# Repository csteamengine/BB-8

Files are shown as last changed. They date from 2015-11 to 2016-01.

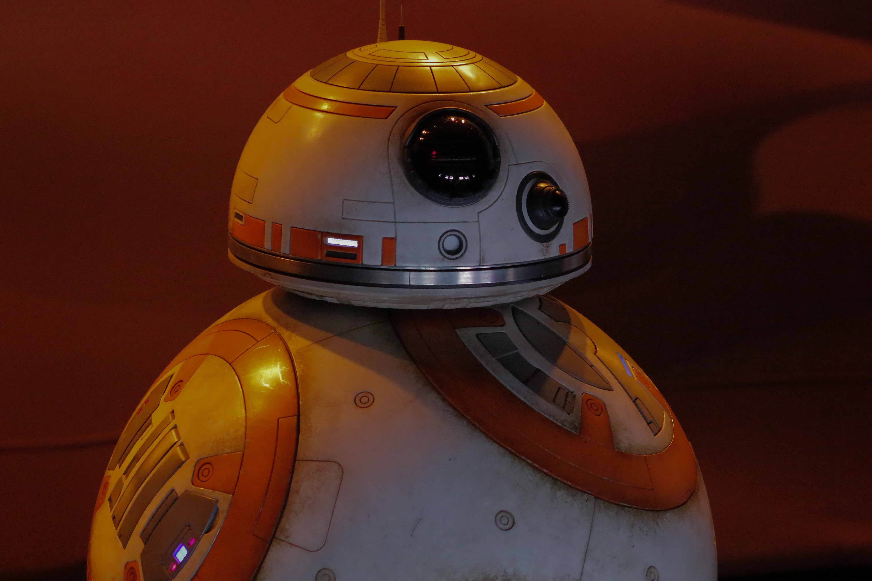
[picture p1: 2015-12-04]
Images/BB-8Reference.jpg

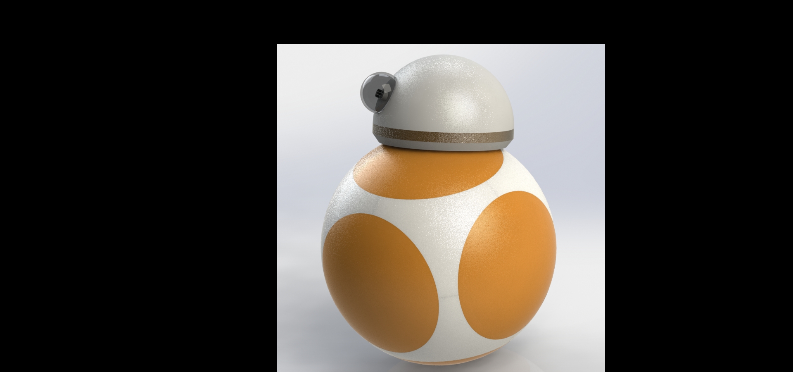
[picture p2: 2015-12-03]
Images/BB-8Early.JPG

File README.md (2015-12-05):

# BB-8
## Our version of BB-8 from Star Wars Episode VII
BB-8 from Star Wars Episode VII, The Force Awakens

For this project, we are attempting to build our own BB-8 as seen in the Star Wars Episode VII. He is a rolling droid with a head that can swivel around as he rolls, without falling off. 

To accomplish this, we used the following hardware...
```
Raspberry Pi 2 B+
2 DC gear motors + wheels
3 servos for head control
Old 12" Globe (main body) //We are working on getting a 3D printed body. Currently designing it.
Strong Magnets
Ball Bearing Casters
Foam Hemisphere for the head
Other Structural pieces of your choice (Ex// K'NEX or popsicle sticks)
Other Items for Decoration
Paint of your choice
```
We used [this](http://www.amazon.com/gp/product/B00GLO5SMY?psc=1&redirect=true&ref_=ox_sc_act_title_1&smid=A3P9EAC3KD93H7) chassis and motor combo.

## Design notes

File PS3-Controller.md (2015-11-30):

#PS3 Controller

The $ denotes the beginning of a line of code to be entered in the Terminal. 
First make sure your Pi is up to date (This may take a while depending on your pi):
	
	$sudo apt-get update
	
Then make install the bluetooth dongle support. This is different for each dongle so I will let you do that part.
There are tutorials all over the place explaining what to do.

Next install the bluetooth support (Drivers, compilers and such) this one will take a long time so get comfortable:   

	$ denotes a new line. this first one is a long line.
	$sudo apt-get install bluez-utils bluez-compat bluez-hcidump checkinstall libusb-dev libbluetooth-dev joystick
      
Once this is done you will need to download and compile the controller utility:

	$wget http://www.pabr.org/sixlinux/sixpair.c
    	$gcc -o sixpair sixpair.c -lusb

Next connect the PS3 controller to the Pi using the USB cable and type the following
    
    	$sudo ./sixpair

If this is successful, it will return something like this:

	Current Bluetooth master: 00:10:60:57:15:C7
 	Setting master bd_addr to: 00:10:60:57:15:C7 

If no controller is connected, a message will pop up saying "No controller found on USB busses". In my experience I only     needed to run the sudo ./sixpair command once for each controller, as long as you haven't reset it. Now run the following 		to download sixad, the controller manager.
    
    	$wget http://sourceforge.net/projects/qtsixa/files/QtSixA%201.5.1/QtSixA-1.5.1-src.tar.gz
    	$sudo tar xfvz QtSixA-1.5.1-src.tar.gz
    	$cd QtSixA-1.5.1/sixad
    	$sudo make
    	$sudo mkdir -p /var/lib/sixad/profiles
    	$sudo checkinstall

Once that is done, run the following to allow the controller mangager to run at boot. Now when you reboot the Pi, sixad will automatically run.

	$sudo update-rc.d sixad defaults
#PS3 Controller
Finally, unplug the controller and reboot the system.

	$sudo reboot

Once it is up and running again, sixad will already be running so all you have to do is press the PS button. If it does not connect or doesnt recognize it, first try restarting sixad.

    	$sudo sixad --stop
    	$sudo sixad --start
    
At this point it will prompt you to press the PS button. When you do so it will display this if it connected successfully.
This will be displayed on the screen.

	sixad-bin[2535]: started
	sixad-bin[2535]: sixad started, press the PS button now
	sixad-bin[2535]: unable to connect to sdp session
	sixad-bin[2535]: Connected Sony Computer Entertainment Wireless Controller

If it still wont connect then try plugging the controller in again and running.

	$sudo ./sixpair

Each time you start the pi, you simply have to press the PS button on the controller to connect it, as long as you ran the update -rc command above. However if you want to connect a second controller on boot up, in the terminal just type 
	$sixad --stop
	$sixad --start
Then press the PS button on the second controller.

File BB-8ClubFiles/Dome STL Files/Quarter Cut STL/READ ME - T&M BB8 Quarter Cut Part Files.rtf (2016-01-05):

For those with smaller X & Y build areas, like the FlashForge, Dremel, MakerBot Mini. Tiny has developed these Quarter Cut pieces.

These work just like the regular pieces, however instead of being 3 pieces to make a complete part, such as Dome Ring, Dome Skirt or even the Dome Panels, it requires you to print all 4 pieces.

The Dome Ring, you will notice is just 1 (one) STL part file, however you will need to print the file 4 times. This is indicated in the file name of the part by the x4 nomenclature.

Where as the Dome Skirt is actually only 2 (two) STL part files, and you will print each of those twice (x4). This is indicated in the file name of the part by the x2 nomenclature.

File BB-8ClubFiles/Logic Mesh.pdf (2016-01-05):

LED Panel Mesh Dome

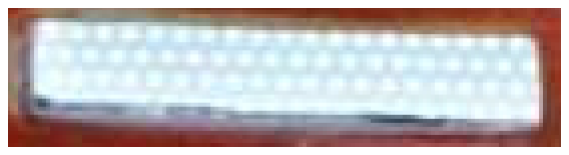
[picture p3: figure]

Approx. 23mm x 4mm

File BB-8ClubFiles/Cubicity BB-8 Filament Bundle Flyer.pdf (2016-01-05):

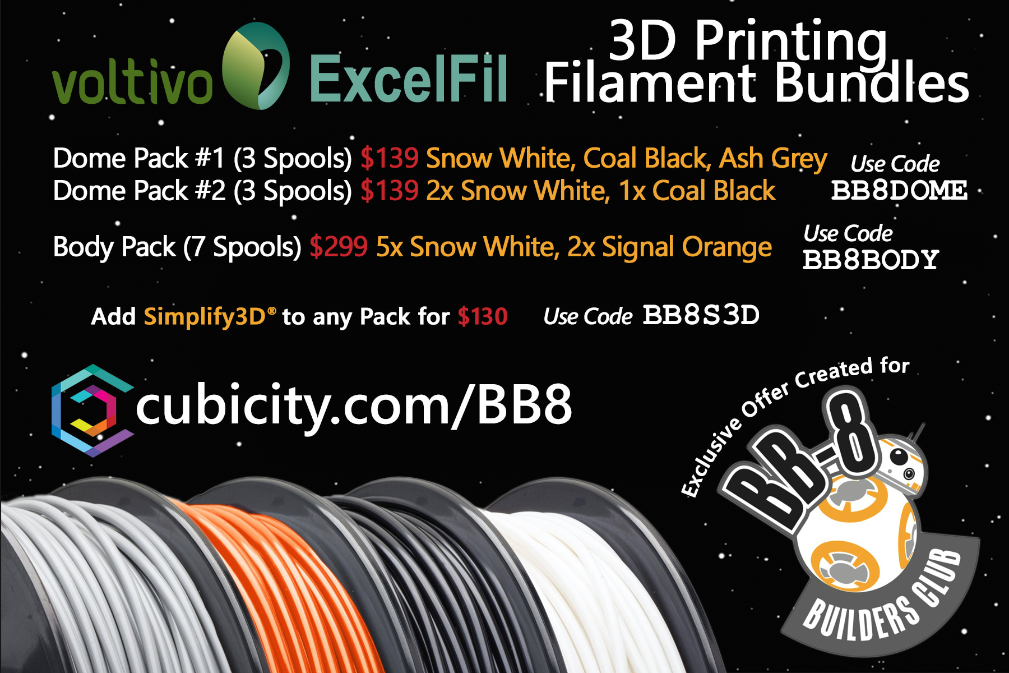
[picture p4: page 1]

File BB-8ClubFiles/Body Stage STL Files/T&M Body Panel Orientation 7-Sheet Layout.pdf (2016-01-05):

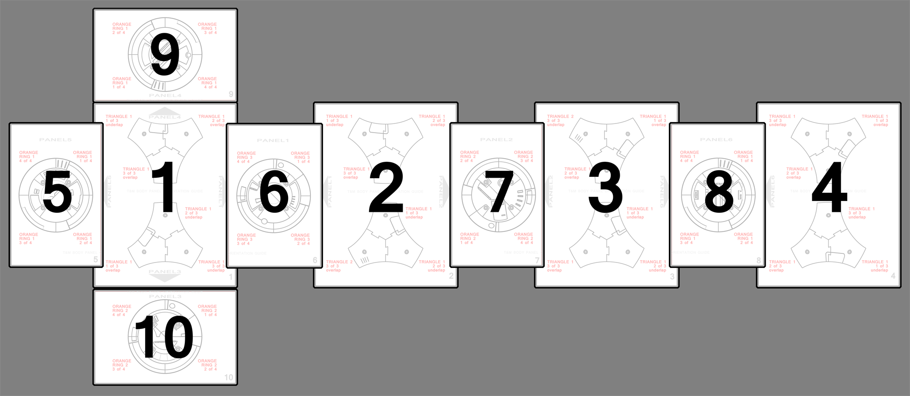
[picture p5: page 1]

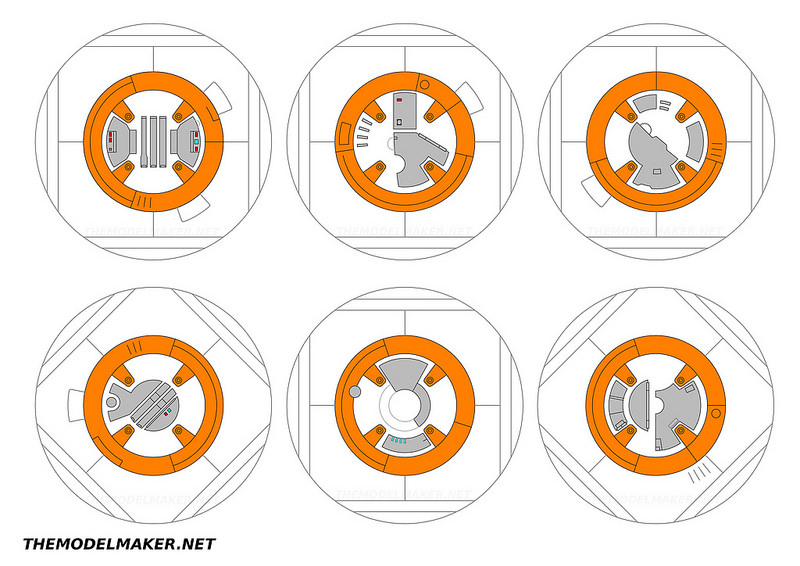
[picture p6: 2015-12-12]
Images/BB-8Panels.jpg

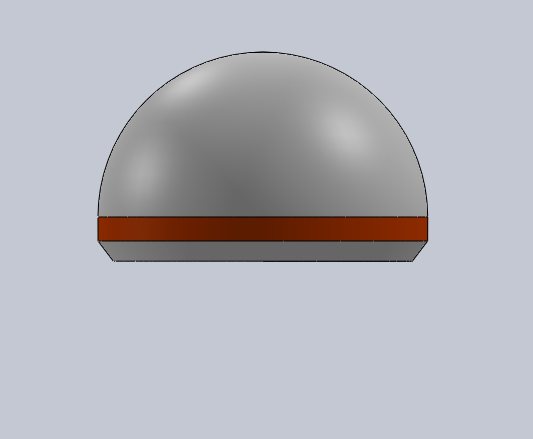
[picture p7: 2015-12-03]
Images/CAD3.PNG

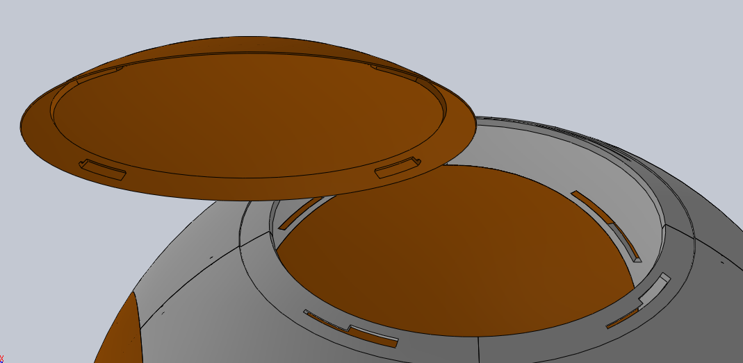
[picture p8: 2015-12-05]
Images/LockingMechanism.PNG

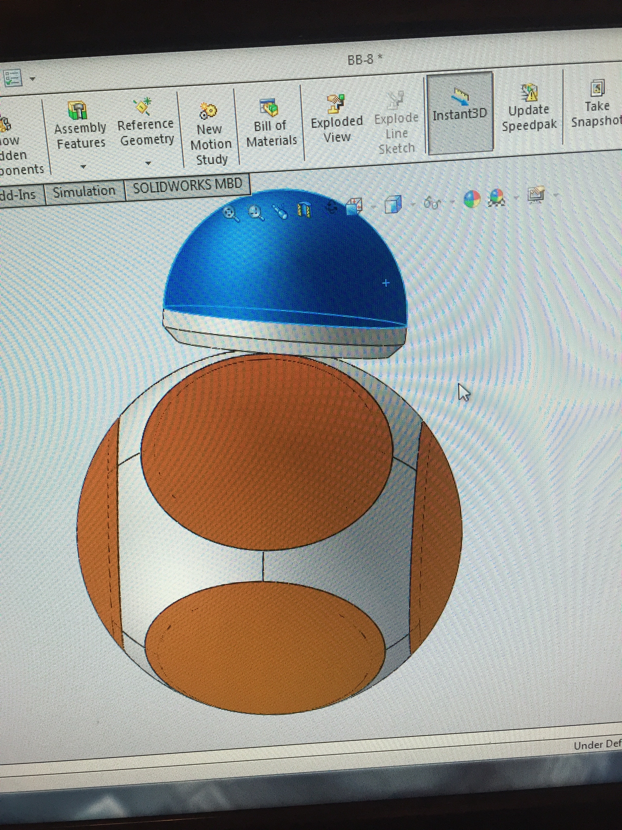
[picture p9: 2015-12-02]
Images/CAD1.jpg

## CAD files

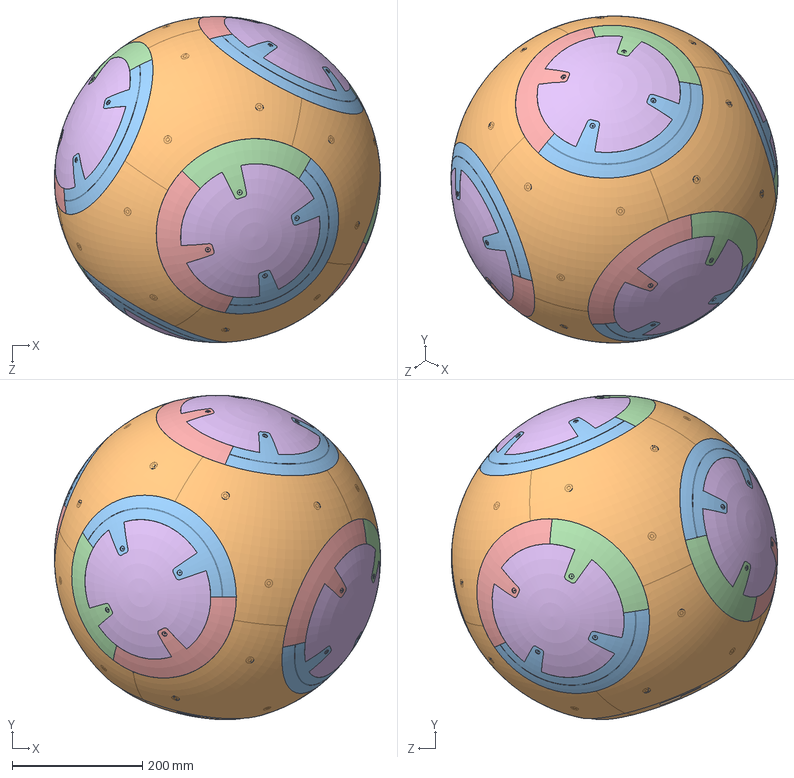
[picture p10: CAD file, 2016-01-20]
CAD/BB-8Test.SLDASM
499.8 x 497.2 x 499.8 mm
BB-8InnerShell x 4
BB-8Shell2 x 8
BB-8Shell1 x 5
BB-8Shell4 x 5
BB-8Shell5 x 5
BB-8Shell6 x 5
BB-8InnerShellTop x 4

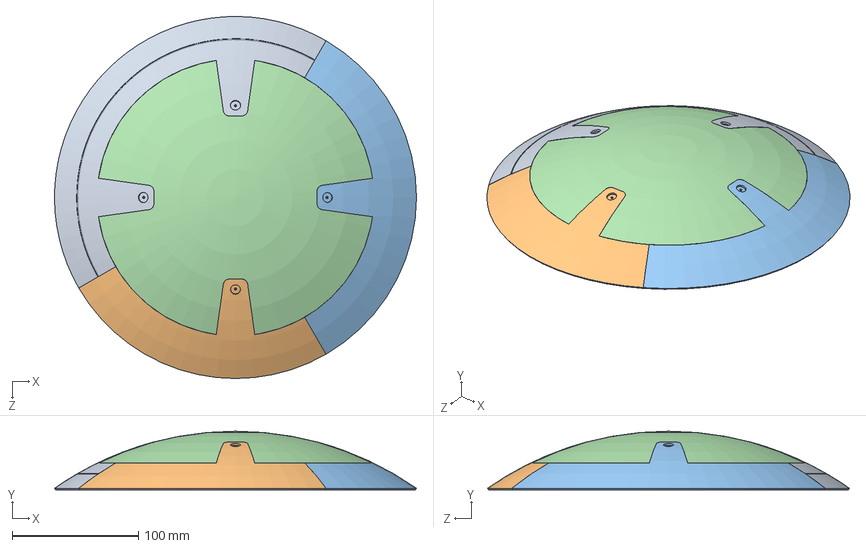
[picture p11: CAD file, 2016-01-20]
CAD/BB-8Panel.SLDASM
286.8 x 46.4 x 286.8 mm
BB-8Shell1
BB-8Shell4
BB-8Shell5
BB-8Shell6

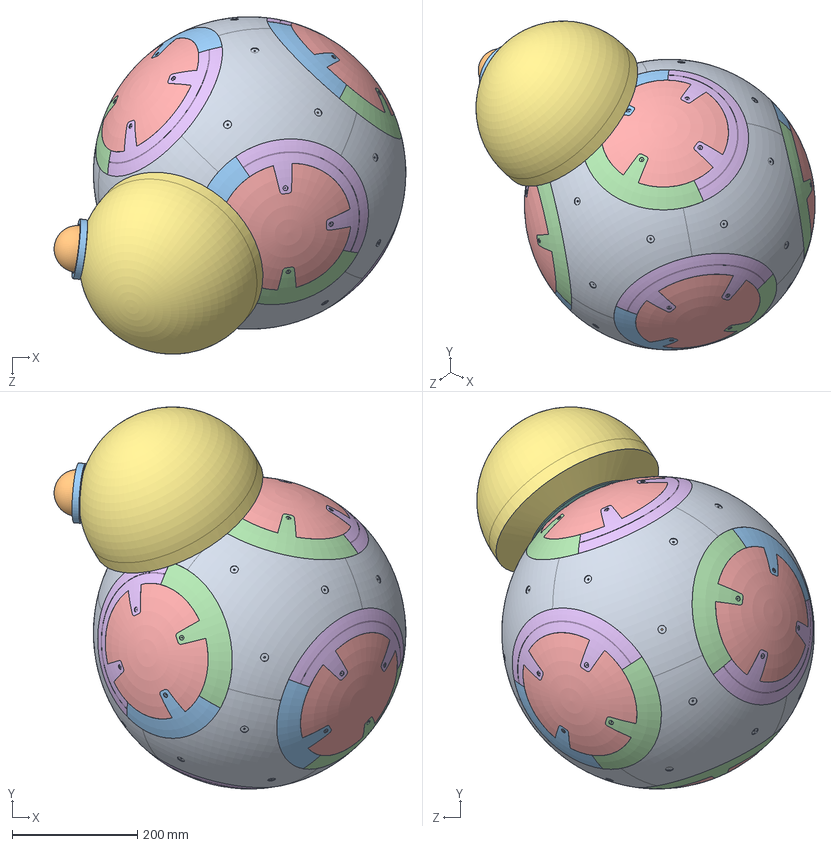
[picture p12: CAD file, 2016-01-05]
CAD/BB-8.SLDASM
562.8 x 611.2 x 539.8 mm
BB-8Shell2 x 8
BB-8Shell3 x 12
BB-8Shell4 x 6
BB-8Shell5 x 6
BB-8Shell6 x 6
BB-8Shell1 x 6
BB-8Head
BB-8HeadBottom
Ball Bearing x 4
BB-8Eye
BB-8EyeCap
Ball-Bearing-Cap x 4

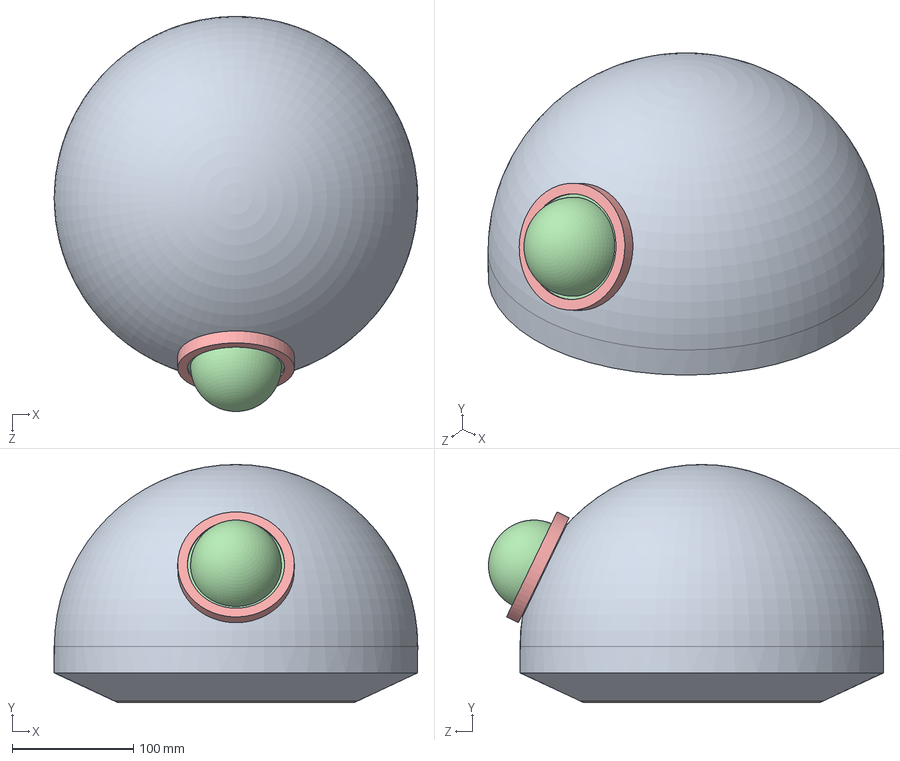
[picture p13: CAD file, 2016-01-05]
CAD/BB-8Head.SLDASM
300.0 x 196.4 x 325.9 mm
BB-8Head
BB-8HeadBottom
Ball Bearing x 4
BB-8Eye
BB-8EyeCap
Ball-Bearing-Cap x 4

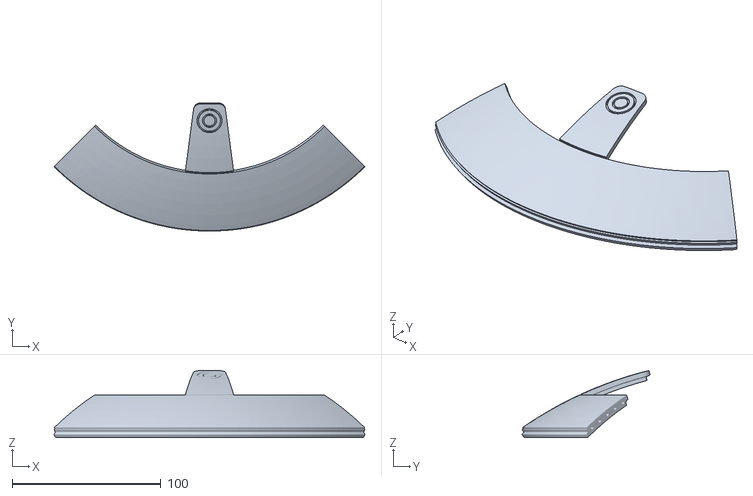
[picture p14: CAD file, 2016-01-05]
BB-8ClubFiles/Body Stage STL Files/Orange Rings/Orange Ring 1 V506mm 4 of 4 -1mm.stl
208.8 x 86.1 x 45.0

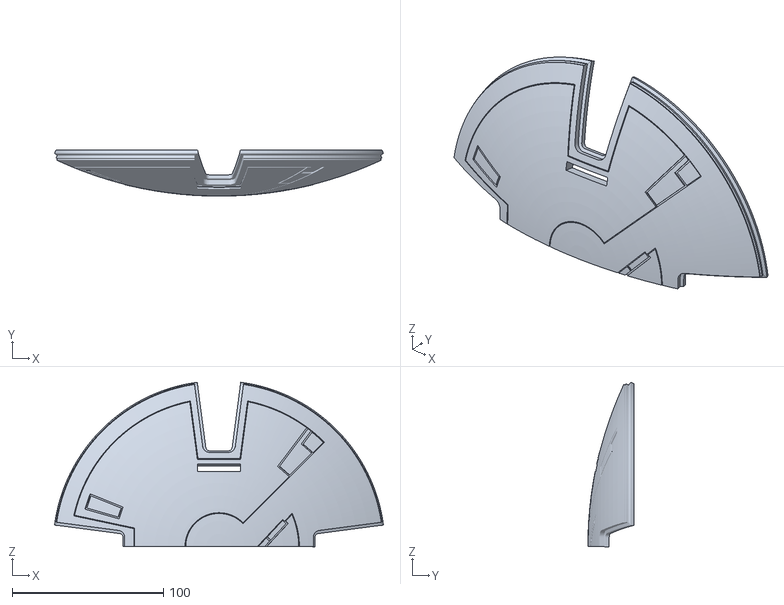
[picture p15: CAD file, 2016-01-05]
BB-8ClubFiles/Body Stage STL Files/Panels/Panel 3 V506mm 2 of 2 -1mm.stl
217.2 x 30.6 x 108.6

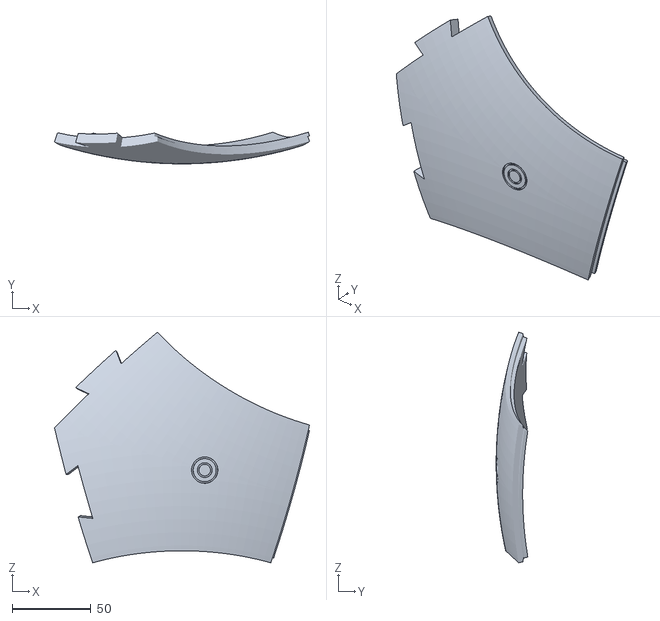
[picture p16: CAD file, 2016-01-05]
BB-8ClubFiles/Body Stage STL Files/Triangles/Triangle1 - 3 of 3 - underlap.stl
162.3 x 20.2 x 146.8

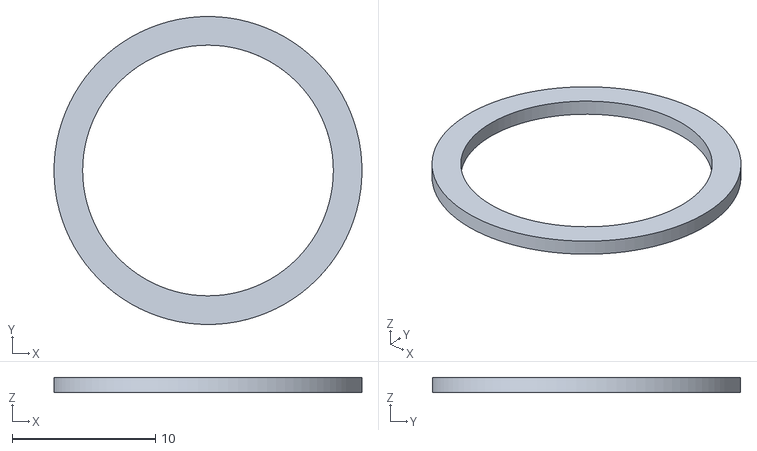
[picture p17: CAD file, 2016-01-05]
BB-8ClubFiles/Dome STL Files/BB8 PSI Ring V1.stl
21.5 x 21.5 x 1.07

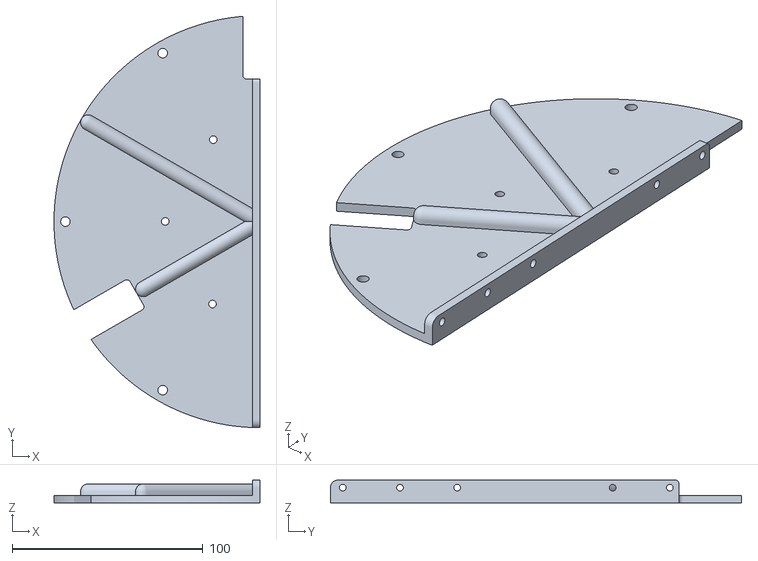
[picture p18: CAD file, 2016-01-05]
BB-8ClubFiles/Dome STL Files/Lite DMM Retro Fit/Upper Plate Lite B v3.stl
108.0 x 215.6 x 12.0

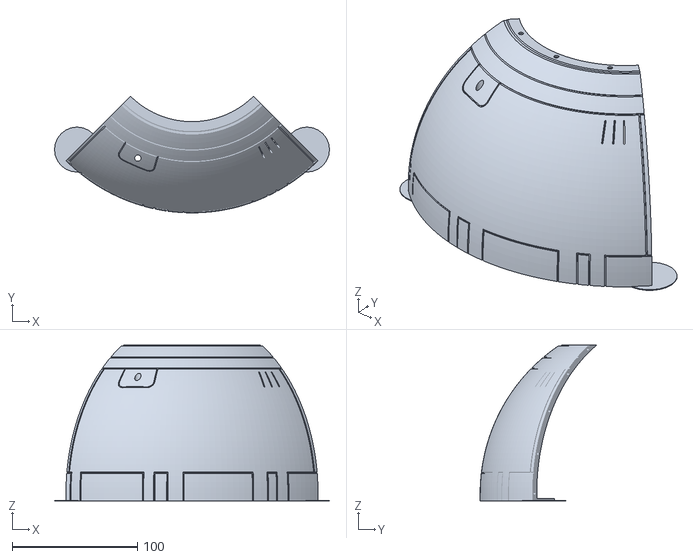
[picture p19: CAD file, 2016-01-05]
BB-8ClubFiles/Dome STL Files/Quarter Cut STL/BB8 Dome Panel 3 Mag QTR.stl
219.8 x 93.3 x 124.6

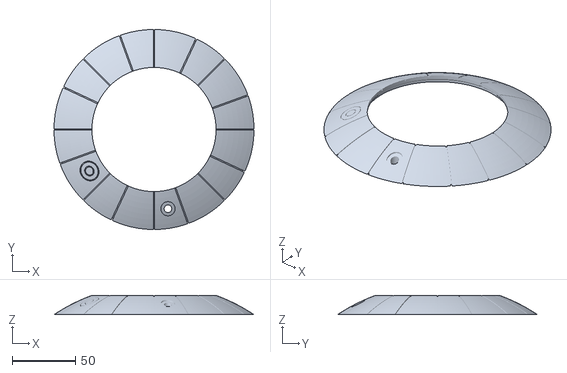
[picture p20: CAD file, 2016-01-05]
BB-8ClubFiles/EXPERIMENTAL/BB-8 Parts for Large Format Printers/Dome Pie Panel 1-Piece.stl
158.0 x 158.0 x 15.2

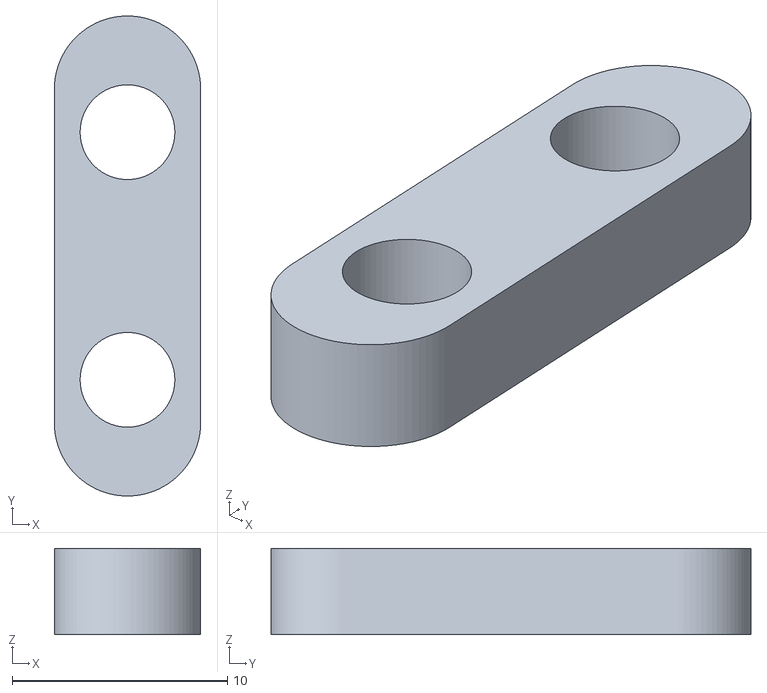
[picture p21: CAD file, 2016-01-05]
BB-8ClubFiles/Hamster/BMM Sides v2.stl
6.80 x 22.3 x 4.00

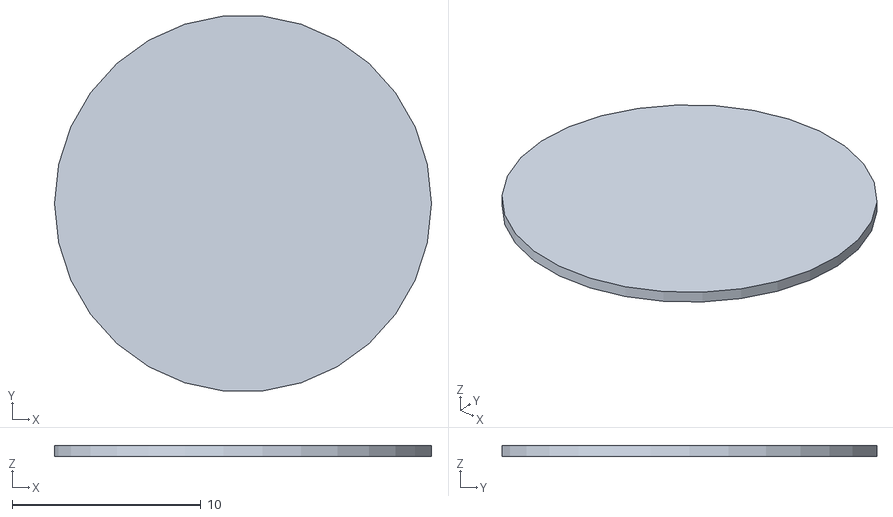
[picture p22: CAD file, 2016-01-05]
BB-8ClubFiles/Helper Disks/Helper_Disk_Small.stl
20.0 x 19.9 x 0.6

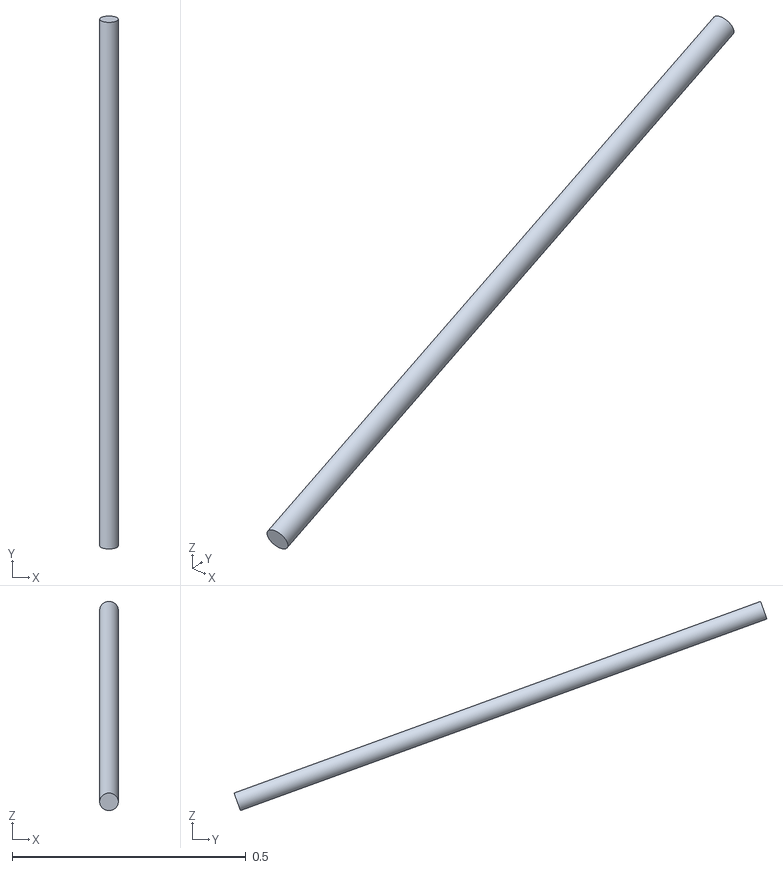
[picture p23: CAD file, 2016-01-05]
BB-8ClubFiles/Ringmaster's Pitch Fork/forkhandle.stl
0.04 x 1.14 x 0.448

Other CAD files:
BB-8ClubFiles/EXPERIMENTAL/Lite DMM Retro Fit/Upper Plate Lite A v3.stl
CAD/Part2.SLDPRT
BB-8ClubFiles/Body Stage STL Files/Orange Rings/Orange Ring 1 V506mm 3 of 4 -1mm.stl
BB-8ClubFiles/Body Stage STL Files/Panels/Panel 5 V506mm 2 of 2 -1mm.stl
BB-8ClubFiles/Body Stage STL Files/Orange Rings/Orange Ring 1 V506mm 1 of 4 -1mm.stl
BB-8ClubFiles/Body Stage STL Files/Orange Rings/Orange Ring 1 V506mm 2 of 4 -1mm.stl
BB-8ClubFiles/Body Stage STL Files/Orange Rings/Orange Ring 2 V506mm 1 of 4 -1mm.stl
BB-8ClubFiles/Body Stage STL Files/Orange Rings/Orange Ring 2 V506mm 2 of 4 -1mm.stl
BB-8ClubFiles/Body Stage STL Files/Orange Rings/Orange Ring 2 V506mm 3 of 4 V2 -1mm.stl
BB-8ClubFiles/Body Stage STL Files/Orange Rings/Orange Ring 2 V506mm 4 of 4 V2 -1mm.stl
BB-8ClubFiles/Body Stage STL Files/Orange Rings/Orange Ring 3 V506mm 1 of 4 -1mm.stl
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

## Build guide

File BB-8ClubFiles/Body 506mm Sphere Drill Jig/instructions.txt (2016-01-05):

This is intended to be cut with 3/4" MDF and the jig is based on using the California Quality Plastics 20" (506mm) hemispehere that is 1/2" thick. They offer a 3/4" as well but I wouldn't recommend using this jig on that since the pin holes should be centered.  

Things to note for machining or how I setup my toolpaths...

I highly recommend using the following website to determine the appropriate speeds for the tools you have:  

http://zero-divide.net/?page=fswizard

1. Small holes around the diameter to use for pins and magnets in the plastic are .125 in diameter.  Set to machine to peck drill to depth of .07501 (you will need to go a little deeper for a perfect hole but I didn't want to hit my spoil board).  I used a .125 drill bit.

1b. Skip this but I used a 90 degree V-bit to put the creative commons image and text on it.  (I really like to label my jigs permanently)

2. 3/4 4-flute end mill used to mill out a .25" deep pocket between the hamster and the outer dome ring.

Last tool..

3. 1/4" 4-flute end mill was used to pocket the strap holes to a depth of .7501

4. 1/4" 4-flute end mill to cut the hamster.  Set the path to cut ON the line.

5. 1/4" 4-flute end mill to cut the part OUTSIDE line.

We've determine the max depth you would want to drill into your CQP hemisphere is a hair over an inch.  Any more and you will go out the sides.  

We're using the following pins:

Low-Strength Dowel Pin; Aluminum, 1/8" Diameter 3/4" Length
McMaster-Carr Part Number: 97325A410  ($6.54/pk of 10) you need two packs.

I also recommend a drill bit stop collar as well to ensure your hand drill goes to the exact depth.

Drill Bit Stop Collar for Drill Bit Size 1/8"
McMaster-Carr Part Number: 8865A11 ($3.04 ea) You only need one

It may be overkill but you may also want to consider getting a proper drill bit and reamer for this application.

Drill Bit: High-Speed Steel Jobbers' Drill bit for Plastic 60 degree point.  Specifically for use on cast acrylic, pvc, nylon, etc.  

Size: 1/8", Overall length 2-3/4", Drilling Depth .9" 
McMaster-Carr Part Number: 27465A81 ($3.47 ea)

I really don't think you need this but...

Reamer: McMaster-Carr Part Number: 2989A11; ($39.80 ea)

Good luck and happy building!

Steele

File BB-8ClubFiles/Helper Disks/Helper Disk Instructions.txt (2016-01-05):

If you're having problems with the edges of your prints peeling, try using Helper Disks!

First, open a model. Then add a Helper Disk from this menu and use the Move tool to move the Helper Disk to one corner of your object, so the disk just slightly overlaps with the corner of the object on the plate.

Use Copy and Paste to create more helper disks, and add one to each corner of your model. Then go ahead and print! The Helper Disks will increase the surface area of your model and help it stick to the platform without peeling. When your print finishes, you can remove the Helper Disks by cutting or peeling them off.

Still having trouble getting your prints to stick? There are some more things to try in our Troubleshooting guide for the Replicator 2X: http://www.makerbot.com/support/replicator2x/troubleshooting

These Helper Disks were designed by Thingiverse user ctheroux: http://www.thingiverse.com/thing:51066

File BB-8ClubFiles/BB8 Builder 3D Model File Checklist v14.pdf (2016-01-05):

# T&M's BB8 Builder 3D Model Part & File Checklist

V014 09-Dec-2015
Please read the printing guide first. This is just a simple checklist to ensure everything is printed.
Dome Parts | | | Filament
Part Description | # of Files Print Qty | Color | Resolution Helpers Support Comments
Antenna 1 (White Upper) | 2 | 1 | White | <0.2mm | YES | No
Antenna 2 (Black Lower - 150mm wire) | 2 | 1 | Black | <0.2mm | YES | No
Antenna 2 (Black Tip) | 1 | 2 | Black | <0.2mm | No | No
Dome Logic Lenses | 1 | 1 | CLEAR | 0.3mm | No | No | 3mm LEDs
Dome Logic Housings (Optional) | 1 | 1 | Black | 0.2mm | No | No
Dome Magnet Mount Lite (aka DMM) | 1 | 1 | White | 0.2mm | No | No
DMM Caster Race | 1 | 3 | White | 0.2mm | No | YES
Dome Panel 1 | 1 | 1 | White | 0.2mm | SPECIAL | YES
Dome Panel 2 | 1 | 1 | White | 0.2mm | YES | YES
Dome Panel 3 | 1 | 1 | White | 0.2mm | YES | No
Dome Plate | 1 | 3 | White | 0.2mm | YES | No
Dome Ring | 1 | 3 | Black | 0.2mm | YES | No
Dome Skirt 1 | 1 | 1 | White | <0.2mm | YES | No
Dome Skirt 2 | 1 | 1 | White | <0.2mm | YES | No
Dome Skirt 3 | 1 | 1 | White | <0.2mm | YES | No
Dome Top | 1 | 1 | White | <0.2mm | YES | YES
Holoprojector | 1 | 1 | Black | <0.2mm | No | No
Holo LED Mount (Optional) - Brian Munger | 1 | 1 | White | 0.2mm | No | No | 3mm LED
Pie Panel Ring | 2 | 1 | Black | <0.2mm | YES | No
PSI Housing | 1 | 1 | Black | 0.2mm | No | No
PSI LED Mount (Optional) - Brian Munger | 1 | 1 | White | 02mm | No | No | 3mm LED
PSI Rear Cover (Optional) | 1 | 1 | Black | 0.2mm | No | No | VADER PSI / 3mm
PSI Ring (Optional) | 1 | 1 | White | 0.2mm | No | No
Radar Internal (Large) | 1 | 1 | Black | 0.1mm | No | No
Radar Eye Surround 1 Piece | 1 | 1 | Black | 0.2mm | No | No
Radar Eye Surround 2 Piece (Optional) | 2 | 1 | Black | 0.2mm | No | No
Radar Eye Lens Cutting tool 68mm | 1 | 1 | Any | 0.2mm | No | No
Hamster Parts | | | Filament
Part | # of Files Print Qty | Color | Resolution Helpers Support Comments
Actuator Sleeves | 1 | 1 | ANY | 0.2mm | NO | NO | 100% Infill
Battery Box Left | 1 | 1 | ANY | 0.3mm | No | YES
Battery Box Right | 1 | 1 | ANY | 0.3mm | No | YES
Body Magnet Mount Arm | 1 | 1 | ANY | 0.3mm | No | No
Body Magnet Mount | 1 | 1 | ANY | 0.3mm | No | No
Tilt Arm | 1 | 1 | ANY | 0.2mm | No | YES | 8 Shells, 30%
Tube Template | 1 | 1 | ANY | 0.2mm | No | No
Weight Spacer | 1 | 1 | ANY | 0.3mm | No | No | 8 Shells, 30%

T&M BB8 Model Files by Tiny Panganiban & Michael Erwin are licensed under a Creative Commons Attribution-NonCommercial-ShareAlike 4.0 International License.

Body "Stage" Parts | | | Filament
Part | # of Files Print Qty | Color | Resolution Helpers Support Comments
Body Panel 1 1 of 3 | 1 | 1 | White | 0.2mm | YES | YES
Body Panel 1 2 of 3 | 1 | 1 | White | 0.2mm | YES | YES
Body Panel 1 3 of 3 | 1 | 1 | Gray/Silver | 0.2mm | YES | YES
Body Panel 2 1 of 2 | 1 | 1 | White | 0.2mm | YES | YES
Body Panel 2 2 of 2 | 1 | 1 | White | 0.2mm | YES | YES
Body Panel 3 1 of 2 | 1 | 1 | White | 0.2mm | YES | YES
Body Panel 3 2 of 2 | 1 | 1 | White | 0.2mm | YES | YES
Body Panel 4 1 of 2 | 1 | 1 | White | 0.2mm | YES | YES
Body Panel 4 2 of 2 | 1 | 1 | White | 0.2mm | YES | YES
Body Panel 5 1 of 2 | 1 | 1 | White | 0.2mm | YES | YES
Body Panel 5 2 of 2 | 1 | 1 | White | 0.2mm | YES | YES
Body Panel 6 1 of 2 | 1 | 1 | White | 0.2mm | YES | YES
Body Panel 6 2 of 2 | 1 | 1 | White | 0.2mm | YES | YES
Triangle1 Piece 1 Overlap | 1 | 3 | White | 0.2mm | YES | YES
Triangle1 Piece 2 Overlap | 1 | 5 | White | 0.2mm | YES | YES
Triangle1 Piece 3 Overlap | 1 | 3 | White | 0.2mm | YES | YES
Triangle1 Piece 1 Under | 1 | 5 | White | 0.2mm | YES | YES
Triangle1 Piece 2 Under | 1 | 3 | White | 0.2mm | YES | YES
Triangle1 Piece 3 Under | 1 | 3 | White | 0.2mm | YES | YES
Triangle2 Piece 3 Overlap | 1 | 1 | White | 0.2mm | YES | YES
Triangle2 Piece 3 Under | 1 | 1 | White | 0.2mm | YES | YES
Orange Ring 1 1 of 4 | 1 | 3 | Orange | 0.2mm | YES | YES
Orange Ring 1 2 of 4 | 1 | 3 | Orange | 0.2mm | YES | YES
Orange Ring 1 3 of 4 | 1 | 3 | Orange | 0.2mm | YES | YES
Orange Ring 1 4 of 4 | 1 | 3 | Orange | 0.2mm | YES | YES
Orange Ring 2 1 of 4 | 1 | 2 | Orange | 0.2mm | YES | YES
Orange Ring 2 2 of 4 | 1 | 2 | Orange | 0.2mm | YES | YES
Orange Ring 2 3 of 4 | 1 | 2 | Orange | 0.2mm | YES | YES
Orange Ring 2 4 of 4 | 1 | 2 | Orange | 0.2mm | YES | YES
Orange Ring 3 1 of 4 | 1 | 1 | Orange | 0.2mm | YES | YES
Orange Ring 3 2 of 4 | 1 | 1 | Orange | 0.2mm | YES | YES
Orange Ring 3 3 of 4 | 1 | 1 | Orange | 0.2mm | YES | YES
Orange Ring 3 4 of 4 | 1 | 1 | Orange | 0.2mm | YES | YES
Body "Static" Parts | | Filament
Part | # of Files Print Qty | Color | Resolution Helpers Support Comments

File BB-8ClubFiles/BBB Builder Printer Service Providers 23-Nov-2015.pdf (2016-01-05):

BB8 Builder Printing Service Providers Last
Updated: | 23-Nov-15
Name | 3D
Printer | Location Filament
| | | | Recommened
| | | | Settings Used | Print
| | | | | Hour Rate
Micke Askernäs | Custom | Sweden | PLA | Yes | $8.00€
Steven Bornhoeft | Ultimaker2 | USA | PLA | Yes | $8.00
Rick McCaskill | Ultimaker Original | CAN | PLA | Yes | $8.60C
Santino Loia | FlashForge Creator | USA | PLA | Yes | $7.00
Brent Picha | ROBO3D | USA | PLA | Yes | $5.00
XLRobots Ameralis MakerBot | USA | PLA | Yes | $5.50
Michael Erwin | MakerBot Rep 2 | USA | PLA | Yes | $6.50

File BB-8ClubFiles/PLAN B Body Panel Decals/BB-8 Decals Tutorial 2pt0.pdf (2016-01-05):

BB-8

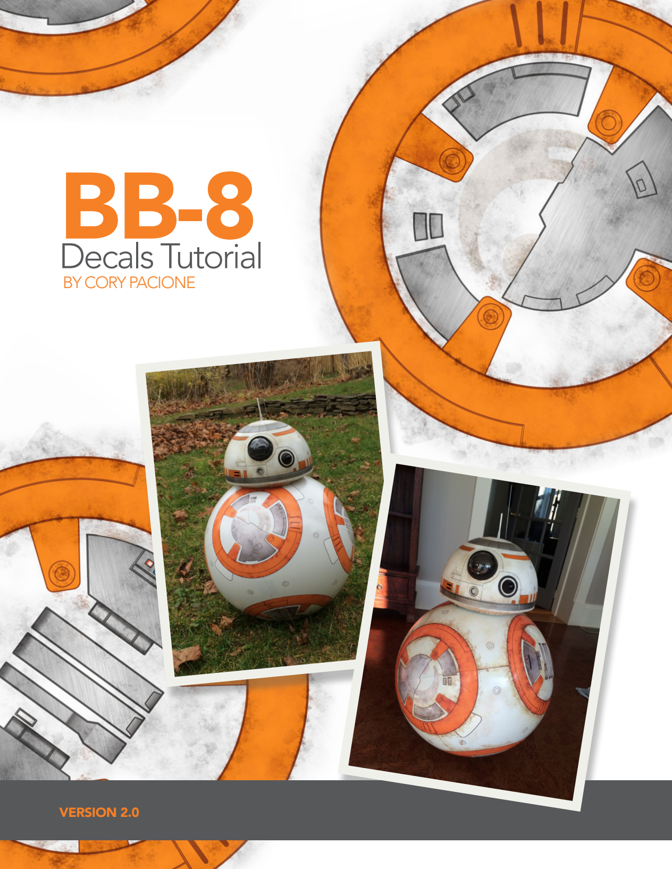
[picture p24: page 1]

# Decals Tutorial

### BY CORY PACIONE

## VERSION 2.0

## PAGE 2

# FORWARD

Before you start your decals installation, please be sure to read through these instructions carefully.

These vinyl wraps are made from the finest automotive grade vinyl. The vinyl is waterproof so you

don’t need to worry about the decals getting wet, etc. That being said, you are attempting to wrap

a SPHEREICAL object with a FLAT DECAL, which can easily cause creases, extra material which

may need be cut away or trimmed, etc. DO NOT ATTEMPT TO INSTALL AS ONE PIECE. It’s

recommended that each orange circle be cut in quarter segments (but not on the seams of where

the hemispheres will meet).

These are time consuming to install and will take great patience. Do NOT panic, take things slow

and you should be able to achieve similar results to what is shown.

NOTE: If you’re looking for a PERFECT droid... this method is probably not for you. This is meant to be a more cost effective and relatively accurate alternative to other methods such as 3-D printed pieces or hand cut panels.

## PAGE 3

# STEP ONE: HAVE EVERYTHING READY

There area few items that you should have on hand for the installation.
c | Scissors
c | Masking Tape
c | Ruler
c | Pencil
c | Compass
c | Duct Tape
c | Panel Diagram (see attached)

In addition to the above items, make sure that you have your hemispheres sanded, primed and painted.

# STEP TWO: MARKING YOUR HEMISPHERES

## DOME PANEL SPACING

To determine the spacing for the circular panels. Measure 20” x 20” square on a piece of cardboard or plywood. Draw an X at the diagonals. Now place ONE of your hemispheres on the layout and mark where the 4 spots are. You now have equally spaced centers for your side panels. From here, take measurements to determine top dead center for the other panel. Once marked, put your
20”

20”

## TOP VIEW

## PAGE 4

two hemispheres together, rotating until you find the best fit (as they may not be perfectly round). Once you find the best fit, mark the second hemisphere from the measurements on the first hemisphere.

Then take measurements to determine top dead center for the second hemisphere. Now you have the centers of ALL 6 panels marked and ready.

# STEP THREE: DRAW ON YOUR PANEL GUIDES

## TOP PANEL

It is recommended that you choose panel 3 (top right in image below), or panel 4 (bottom left in image below) as the panels for the top of each hemisphere. Then you won’t need to slit the orange tabs along the seams.

## SIDE VIEW

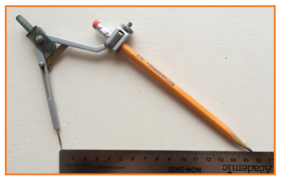
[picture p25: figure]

## PAGE 5

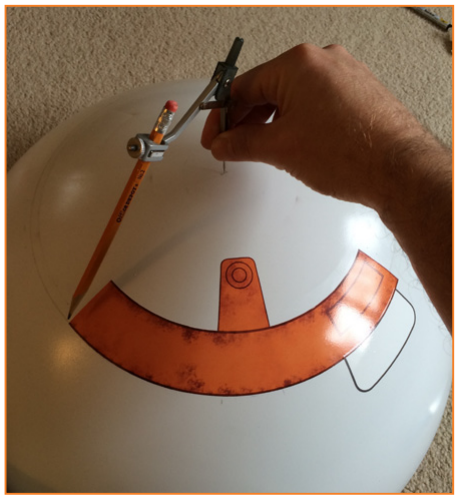
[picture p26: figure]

## GRAB YOUR COMPASS

You’re going to need guides for each panel installation. As mentioned, we’re trying to wrap a flat sheet around a spherical object... so it’s going to be tricky. There WILL BE excess pieces of the orange circle that you’ll either be OVERLAPPING or TRIMMED away. Set your compass to 155mm and then draw the guide circle on the hemisphere.

## IMPORTANT: Once

you have your guide
circle drawn on. Mark
where the 4 orange
tabs will be placed
(evenly spaced quarters). When installing each quarter section, make sure the orange tabs align with the marks of where they should be and work your way out.

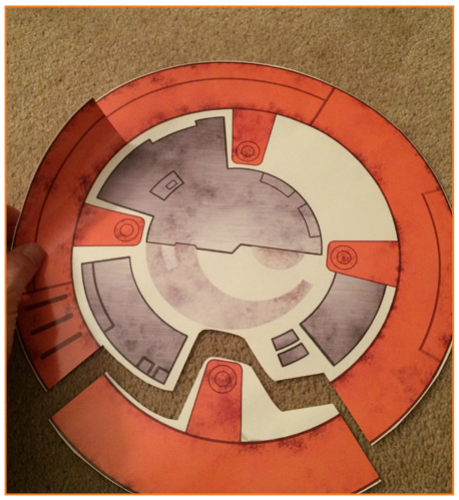
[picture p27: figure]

# STEP FOUR: INSTALLING THE DECALS

Cut each circle out from the main sheet to make it easier to handle. Weed the extra sticker portion (that you don’t need from each sheet) so that you’re only left with the actual decal on the backing paper. Then roughly cut around the circle and determine where you’d like to cut it into sections (quarter sections are recommended).

Choose places on the decals where overlapping won’t interfere with the design. Check out each circle to see where the best place to cut would be.

## MARK THE GUIDES

## CUT INTO SECTIONS

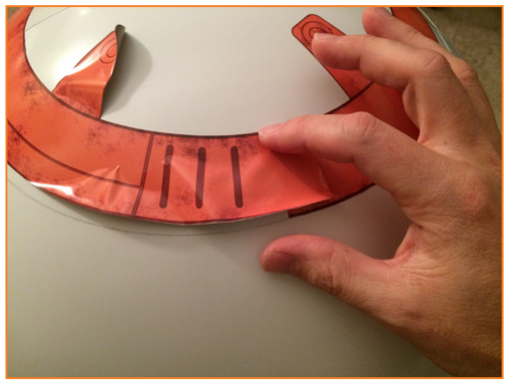
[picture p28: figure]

## PAGE 6

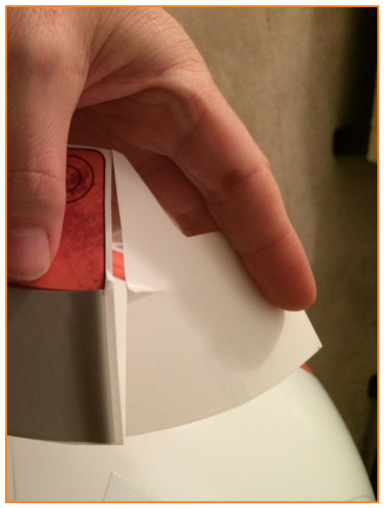
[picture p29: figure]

## THE ORANGE QUARTER SECTIONS

Ok, it’s very important that you don’t press the decal down too tight when you’re placing it on until you know it’s in the right place. remove the backing paper from a section of the piece and position it where you want it. Once you’ve got it started, then remove the rest of the backer paper and SLOWLY work your way across the rest of the decal moving from the center outwards to avoid creasing.

If you do get a crease, simply pull the decal back and try again. DO NOT PANIC. The decal is meant to have some play involved during installation. Take
your time and DO NOT RUSH installation.

See below for examples of how the label COULD look if you try to rush things... and this one eventually went on great.

## REMOVE BACKER IN STAGES

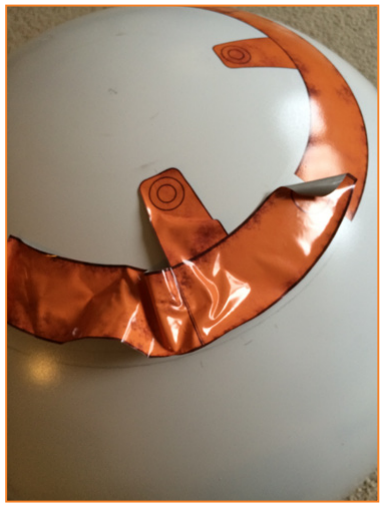
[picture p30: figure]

## WORK YOUR WAY OUT

## DON’T PANIC

## PAGE 7

Continue to follow your guidelines around with the orange sections... and remember that there will be overlap or pieces that you will need to trim out.

## THE METAL DETAIL SECTIONS

Once you’ve got the first orange circle on. Then check the layout diagram and install the center (metal looking) sections. You should find that these are much easier to install. Work your way out from the center of each piece you install to avoid creases.

## REMOVE BACKER IN STAGES

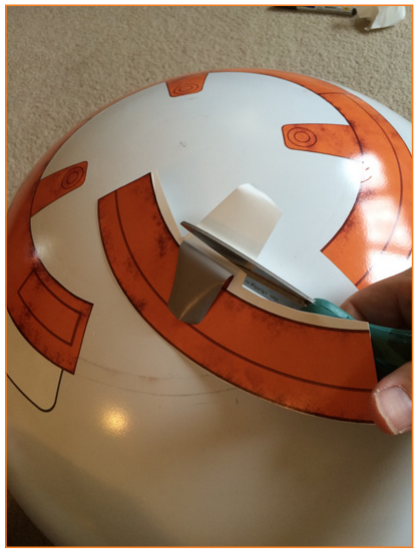
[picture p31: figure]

## INSTALLING THE INNER PIECES

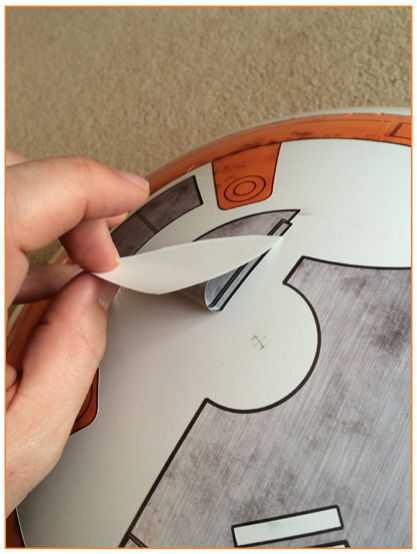
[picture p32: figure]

## PAGE 8

Once you’ve got the first circle panel completed, next move onto the top panel on the second hemisphere. Follow the same instructions.

Once the top of each hemisphere has been completed, duct tape the hemispheres together in a few spots and draw on the remaining 4 circle guides. Then remove duct tape from those areas and install the remaining 4 panels while the ball is taped together. DO NOT slit the labels along the seam. Wait until the entire ball has been completed and then you can use an exacto knife to cut carefully along the seam. Then go over each hemisphere and press the decals firmly to make sure all decals are pressed firmly in place.

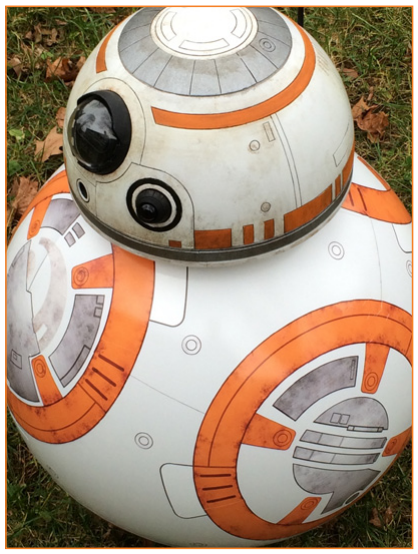
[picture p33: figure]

## THE OTHER DETAILS

Once you’ve got all 6 panels on, you can then add the little side sections to the circles that require it (see attached diagram to see placement for these pieces. You will need to trim off the inner line and then position them in place.

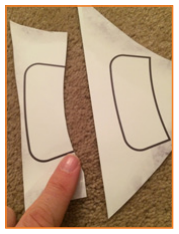
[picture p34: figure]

Once all of those are on. Draw on panel lines to give the illusion of separate panels. Then measure for where to place the small little sensor circles. This was the most fun part as it really gives it the finished look.

## DUCT TAPE TO HOLD TOGETHER

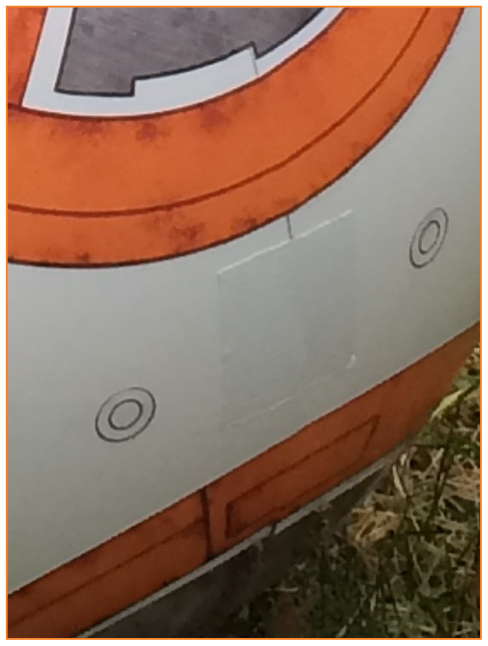
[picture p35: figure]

## INSTALLING THE INNER PIECES

# STEP FIVE: WEATHERING

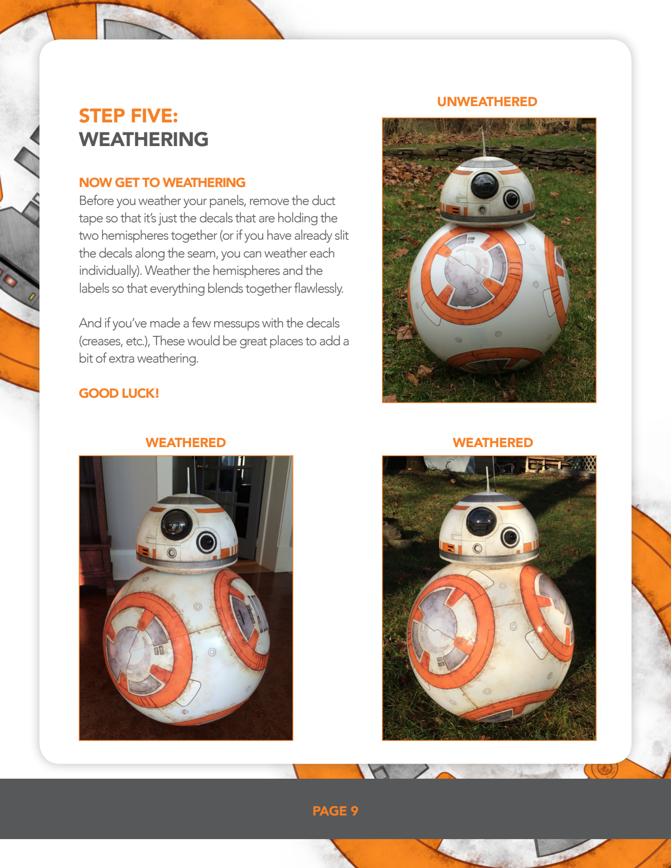
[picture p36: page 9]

## PAGE 9

## NOW GET TO WEATHERING

Before you weather your panels, remove the duct tape so that it’s just the decals that are holding the two hemispheres together (or if you have already slit the decals along the seam, you can weather each individually). Weather the hemispheres and the labels so that everything blends together flawlessly.

And if you’ve made a few messups with the decals (creases, etc.), These would be great places to add a bit of extra weathering.

## GOOD LUCK!

## UNWEATHERED

WEATHERED | WEATHERED

# PANEL DIAGRAM

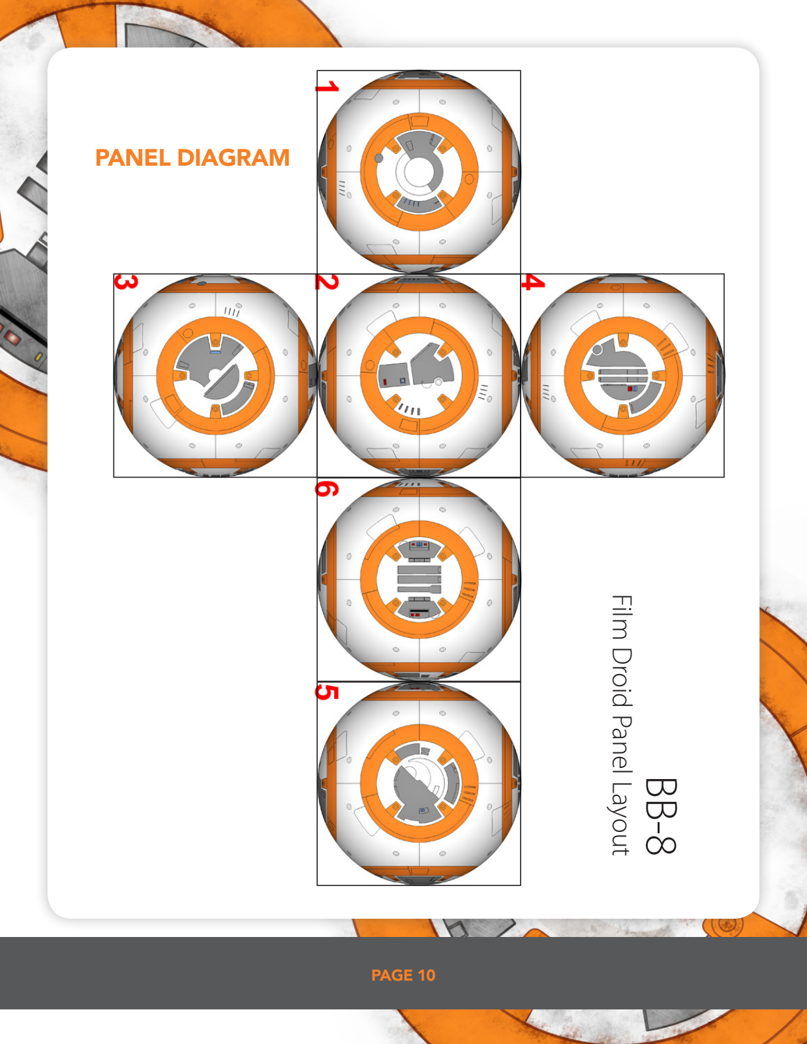
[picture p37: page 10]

## PAGE 10

BB-8

# Film Droid Panel Layout

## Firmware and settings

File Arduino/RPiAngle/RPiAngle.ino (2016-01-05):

#include <Servo.h>
Servo angleServo;
int anglePin = 9;
int angle = 90;
float RU;

void setup() {
  Serial.begin(9600);
  angleServo.attach(anglePin);
}

void loop() {
  if(Serial.available() >0){
    RU = Serial.parseFloat();
  }else{
    RU = 0.0;
  }
  angle = 90 + (RU * 20);
  angleServo.write(angle);
  delay(30);
  Serial.println(RU,angle);
}

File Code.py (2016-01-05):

import time
import serial
import pygame
import RPi.GPIO as GPIO
ser = serial.Serial('/dev/ttyACM0',9600)
GPIO.setmode(GPIO.BCM)
GPIO.setup(23, GPIO.OUT)
motor1 = GPIO.PWM(23,100)
motor1.start(0)
GPIO.setup(24, GPIO.OUT)
motor2 = GPIO.PWM(24,100)
motor2.start(0)
GPIO.setup(4,GPIO.OUT)
GPIO.setup(17,GPIO.OUT)
GPIO.setup(27,GPIO.OUT)
GPIO.setup(22,GPIO.OUT)
pygame.init()
pygame.joystick.init()
clock = pygame.time.Clock()
done = False
LMA = 0
RMA = 0
motorOn = True
toArduino = 90
print("Script Loaded")
while done == False:
    for event in pygame.event.get():
         if event.type == pygame.QUIT:
                 done = True
    controller = pygame.joystick.Joystick(0)
    controller.init()
    RU = controller.get_axis(3)
    RS = controller.get_axis(2)
    LU = controller.get_axis(1)
    LS = controller.get_axis(0)
    L2 = controller.get_button(8)
    R2 = controller.get_button(9)
    R1 = controller.get_button(11)
    L1 = controller.get_button(10)
    Up = controller.get_button(4)
    Down = controller.get_button(6)
    Start = controller.get_button(3)
    Select = controller.get_button(0)
    PS = controller.get_button(16)
    X = controller.get_button(14)
    if LU < 0:
        GPIO.output(4, GPIO.HIGH)
        GPIO.output(17,GPIO.LOW)

        GPIO.output(27, GPIO.HIGH)
        GPIO.output(22,GPIO.LOW)
    if LU > 0:
        GPIO.output(4, GPIO.LOW)
        GPIO.output(17,GPIO.HIGH)
        
        GPIO.output(27, GPIO.LOW)
        GPIO.output(22,GPIO.HIGH)

    if RMA > 100:
        RMA = 100
    if LMA > 100:
        LMA = 100
    if RMA < 40 and RMA != 0:
        RMA = 40
    if LMA < 40 and LMA !=0:
        LMA = 40
    
    LMA = 100 * abs(LU)
    RMA = 100 * abs(LU)
    if L1 == 1:
        LMA = 0
    if R1 == 1:
        RMA = 0

    if motorOn == True:
        motor1.ChangeDutyCycle(LMA)
        motor2.ChangeDutyCycle(RMA)
    if motorOn == False:
        motor1.ChangeDutyCycle(0)
        motor2.ChangeDutyCycle(0)
    RU = round(RU,2)
    ser.write(str(RU))
    print(ser.readline(), RU)
    if L1 ==1 and R1 == 1 and R2 == 1 and L2 ==1:
         done = True
         print("Done!")
    if X == 1:
        print "BEE BEE DOH"
    if Start == 1:
        motorOn = False
        print "motors Off"
    if Select == 1:
        motorOn = True
        print "motors On"
    clock.tick(30)
motor1.stop()
motor2.stop()
GPIO.cleanup()
pygame.quit()

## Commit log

2015-12-02 Added Images folder and CAD folder
2015-12-03 Added solidworks files
    [BB-8.SLDASM, BB-8Head.SLDPRT, BB-8Shell1.SLDPRT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]
2015-12-03 Added a few renders
    [BB-8.SLDASM, BB-8Head.SLDPRT, BB-8Shell2.SLDPRT]
2015-12-03 Added an eye and some color changes. Took a couple renders of full assembly.
    [BB-8.SLDASM, BB-8Eye.SLDPRT, BB-8Head.SLDPRT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]
2015-12-04 Resized a little bit and there are some errors. Will fix later.
    [BB-8.SLDASM, BB-8Shell1.SLDPRT, BB-8Shell2.SLDPRT]
2015-12-05 Added locking mechanism
    [BB-8.SLDASM, BB-8Shell1.SLDPRT, BB-8Shell2.SLDPRT]
2015-12-05 Did some serious work on getting the droid to actually be assemble-able. The bottom of the head screws on, and the ball bearings can poke through. The shell can be constructed similar to a hamsters b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
    [BB-8.SLDASM, BB-8Head.SLDPRT, BB-8HeadBottom.SLDPRT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]
2015-12-05 Don't need BearingHolder anymore
    [BearingHolder.SLDPRT]
2015-12-06 Added a bunch of code to make motors light up when left joystick is pushed up or to the side.
2015-12-08 Forgot to close CAD files before commiting. It always adds the ~BB-8.sld files. Dont want those.
    [BB-8.SLDASM]
2015-12-10 Added a couples sounds
2015-12-16 Added brackets to the inside of the shell that will keep the shell pieces together hopefully better than the peg system I had before.
    [BB-8.SLDASM, BB-8EyeCap.SLDPRT, BB-8Shell2.SLDPRT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]
2015-12-17 Scaled the whole thing down a bit to .8X. If I decide to scale it back up, just go 1.2X. Should fix it.
    [BB-8.SLDASM, BB-8Eye.SLDPRT, BB-8EyeCap.SLDPRT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]
2015-12-17 Separated the shell panels into pieces that can be assembled. not quite done yet.
    [BB-8.SLDASM, BB-8Panel.SLDASM, BB-8Shell1.SLDPRT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]
2015-12-18 Made separate assemblies of the head, panel, and a complete assembly. Need to add threads to a lot of stuff.
    [BB-8.SLDASM, BB-8Eye.SLDPRT, BB-8EyeCap.SLDPRT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]
2015-12-22 added all the BB-8 Builder 3D printing files. Might not use them because they are so big. Definately a good reference though for how things can be put together.
    [BB8 Antenna 1 1of2 V3.stl, BB8 Antenna 1 2of2 V3.stl, BB8 Antenna-2 Base-1.stl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]
2016-01-11 added inner lining to BB-8 Shell
    [BB-8InnerShell.SLDPRT, BB-8Panel.SLDASM, BB-8Shell2.SLDPRT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]
2016-01-20 Worked on Test assembly
    [BB-8InnerShell.SLDPRT, BB-8InnerShellTop.SLDPRT, BB-8Panel.SLDASM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]
2016-01-20 removed autosave files
    [Part2.SLDPRT]
